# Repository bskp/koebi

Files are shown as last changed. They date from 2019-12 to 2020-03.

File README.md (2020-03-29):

Köbi: Robotic Puppeteering
==========================

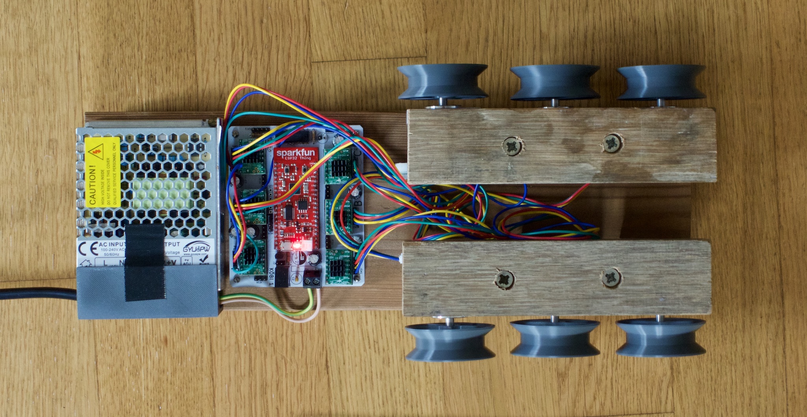
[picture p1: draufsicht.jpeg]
Setup


Köbi is a 6-channel wireless stepper controller consisting of a [SparkFun ESP32 Thing](https://www.sparkfun.com/products/13907) (red) and a **breakout shield** (white). The latter is inspired by [RAMPS](https://reprap.org/wiki/Arduino_Mega_Pololu_Shield) and accomodates six stepper motor drivers ([TMC2130 StepSticks](https://shop.watterott.com/SilentStepStick-TMC2130), green), optical endstop sensors and fan control.

The software on the ESP32 provides an [OSC (Open Sound Control)](https://en.wikipedia.org/wiki/Open_Sound_Control) server. This, in combination with a matching tablet GUI for the modular [TouchOSC](https://hexler.net/products/touchosc) app allows easy control of the steppers (which are the six thread spools).

Alternatively, the module can be controlled by any other OSC client. The OSC endpoints are documented at the [end of this page](#osc-api).

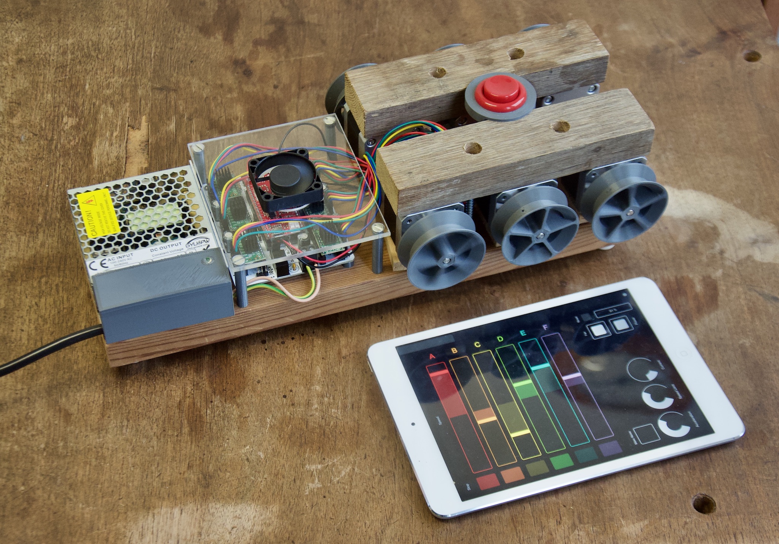
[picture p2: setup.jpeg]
No strings attached!

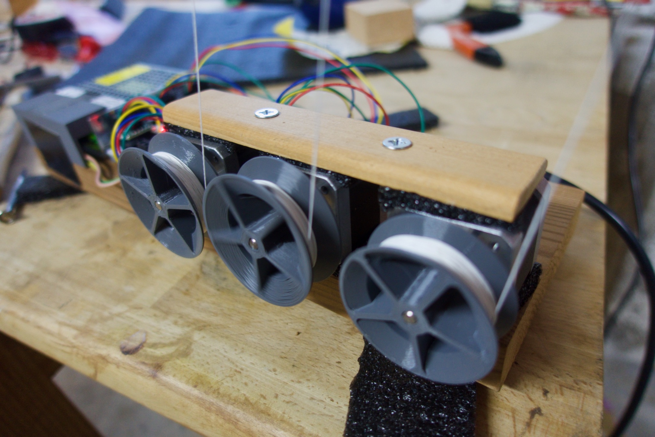
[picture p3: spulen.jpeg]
Spindles with threads


Features
--------

- 500g per thread
- Velocities up to 2m/s
- Wireless control
- Sub-centimeter precision
- (Almost) unlimited thread lengths
- Position and speed feedback for every channel
- Self-calibration using optical markers on the threads (TODO)
- Motor drivers configured using SPI, allowing for:
    - Microstepping reconfiguration (during operation)
    - Current control
    - Load estimation (TODO)
    - Count of missed steps if overload occurs (TODO)
- Easily extendable code written in [Micropython](https://micropython.org)
- Wireless console (WEBREPL) and code update (FTP)
- Additional I2C / SPI / GPIOs broken out

There are a ton of things you can hook it to. Feel free to reuse!

Software + Firmware
-------------------

The ESP32-Board runs a **special build** of the Micropython firmware due to two requirements:

- The PWM hardware module, which generates the **pulses for the  stepper motors**, is currently not supported by Micropython. This special build includes a Python module supporting it, implemented in C: The [MCPWM](https://github.com/bskp/micropython_esp32_mcpwm) module.

- The Python module for the **Trinamic TMC steppper drivers** (which holds names and descriptions to dozens of its registers) had to be frozen in order to save memory: The [TMC]() module. (TODO: Not published yet)

How much do you need? To get you started with the software, each of this three guides covers a different level:
1. **[Getting started](getting_started.md)**: Setup and interact with Köbi _using a tablet_ and the default OSC API
2. **[Hacking](hacking.md)**: Extend Köbis functionality _by modifying the Micropython_ code running the ESP32
3. **[Developing](developing.md)**: Modify the _Micropython firmware (written in C)_ to improve on the modules [MCPWM]() or [TMC](). These are part of the modified Micropython built, ie. "frozen"

Hardware
--------

This repo also supplies you with everything needed to build your own Köbi.

### Bill of Ordering Materials

| Thing | Brand | Part | Source | Price |
|---|---|---|---|---|
| Steppers (5-pack) | Hanpose  | 17HS4401  | AliExpress | 38.-  |
| Voltage Supply (120W) | GYU&PW | S-120-24  | AliExpress | 13.-  |
| ESP32 Thing | SparkFun | DEV-13907 | [bastelgarage](https://www.bastelgarage.ch/sparkfun-esp32-thing) | 22.- |

SN74LS138N

- bom: steppers, supply, esp32, tmcs, pcb/components, wall plug

### 3D Printed Parts
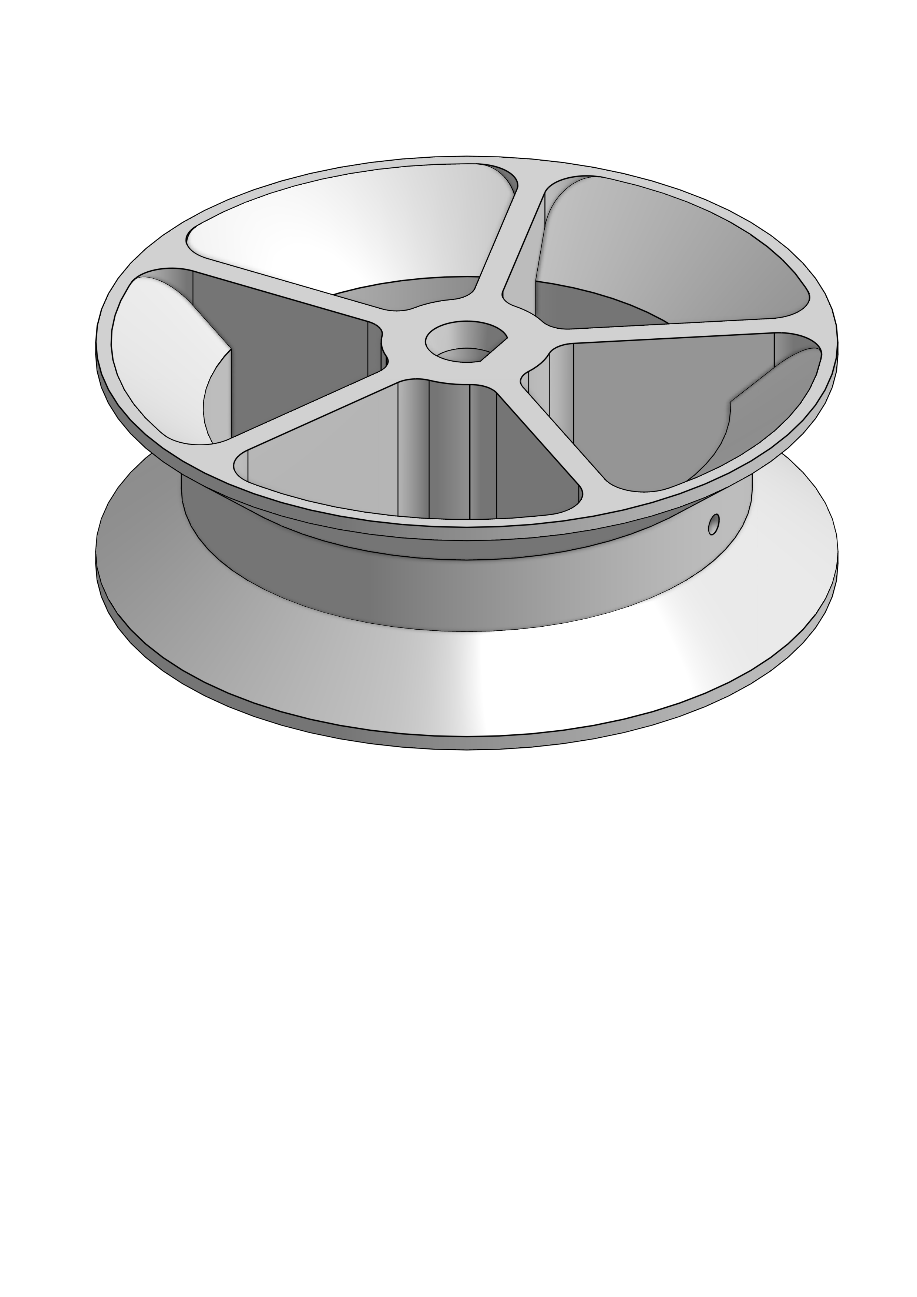
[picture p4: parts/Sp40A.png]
Thread Spool (40mm)

**Thread Spool (40mm)**: [.stl](parts/Sp40A.stl)
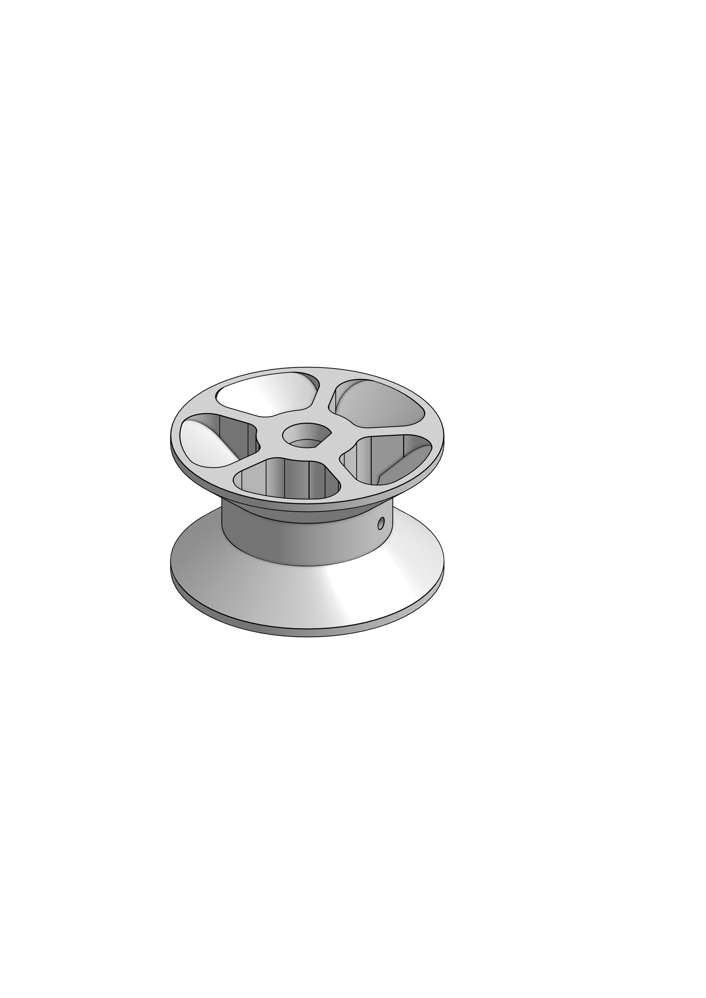
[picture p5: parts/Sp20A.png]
Thread Spool (20mm)

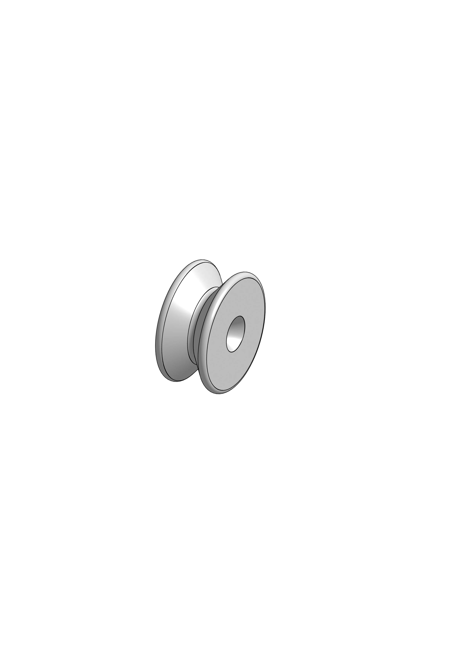
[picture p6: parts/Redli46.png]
Pulley

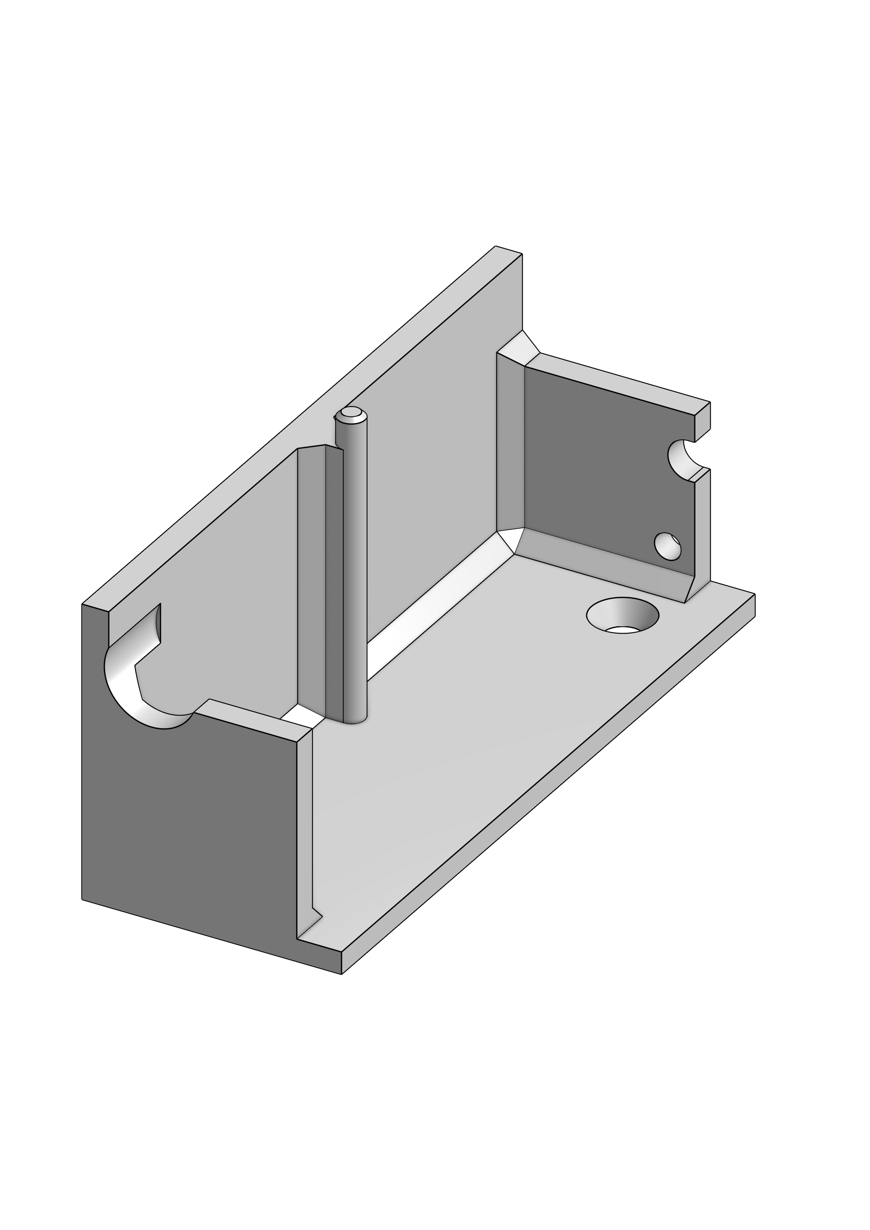
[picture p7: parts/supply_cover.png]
Voltage Supply Cover

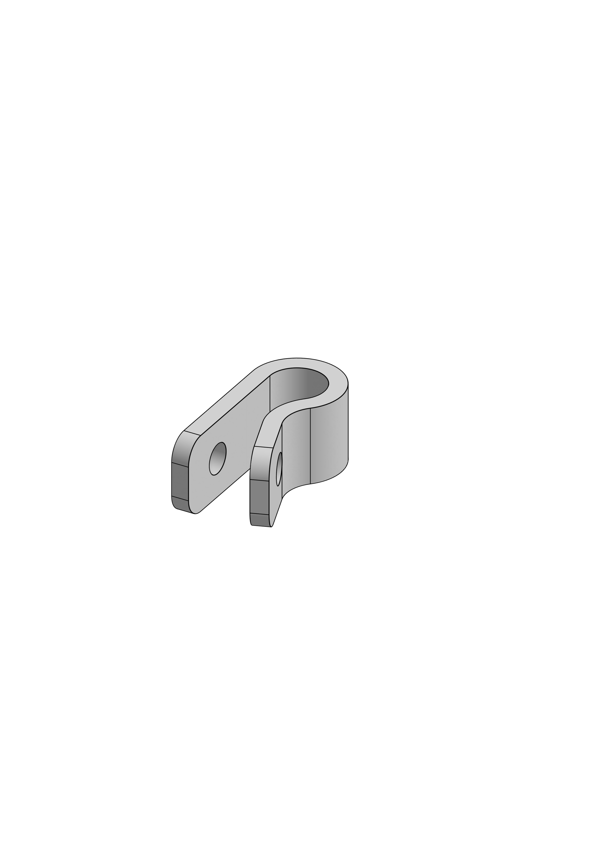
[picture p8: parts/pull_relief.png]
Pull Relief

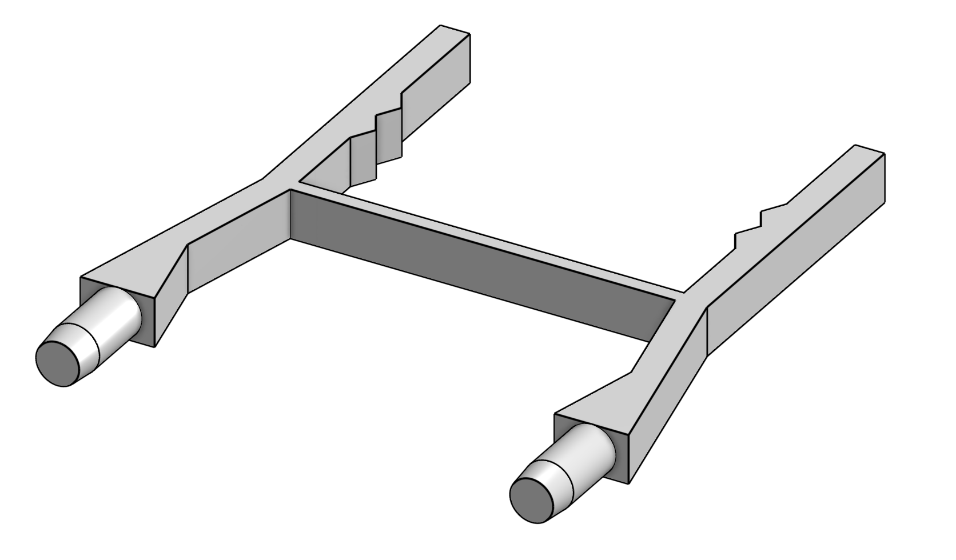
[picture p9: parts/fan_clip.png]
Poor Man's Fan Holder


- stl, link zu onshape

### Printed Circuit Board
- PCB-Daten als pdf, gerber und kicad.

Ideas
-----

- [x] Coordinated 2-axis movements
- [ ] Load visualization
- [ ] Presets with persistent storage
- [ ] Self-calibration with markers
- [x] Sequencer (Sine and jitter movements)
- [x] Coordinated movements for more than 2 axes
- [ ] Inverse kinematics

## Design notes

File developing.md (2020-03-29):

# Extend the Micropython Firmware

If you want to "freeze" a python module to free up RAM, or if you want to extend any of the frozen/native modules ``TMC`` or ``MCPWM``, you'll need to re-compile the firmware.

The process is fully described in the [esp32 port's README.md](https://github.com/micropython/micropython/blob/master/ports/esp32/README.md), but is mostly already taken care of. Start by initializing this repo's submodules:

~~~ bash
$ git submodule update --init --recursive
~~~

This clones the nested repos at ``/firmware/frameworks/``, which are the following projects:

### Micropython
The [referenced micropython fork](https://github.com/bskp/micropython_esp32_mcpwm/tree/micropython-for-koebi) supports the ESP32's **MCPWM**-Module, standing for _Motor control Pulse-Width-Modulation_. This was required to have enough PWM outputs available (6 modules).  
Read more about the MCPWM in [Espressif's API documentation](https://docs.espressif.com/projects/esp-idf/en/latest/esp32/api-reference/peripherals/mcpwm.html)!

### ESP-IDF
For better MCPWM-frequency update behaviour, we use a [minimally modified](https://github.com/espressif/esp-idf/compare/release/v3.3...bskp:dev-mcpwm-synched-updates) variant of the esp-idf, v3.3.1.

The _Micropython ESP32 port_'s Makefile located at ``firmware/frameworks/micropython/ports/esp32`` should already have the correct commit referenced, which was checked out while initializing the submodules:

~~~ Makefile
...
# The git hash of the currently supported ESP IDF version.
# These correspond to v3.3.1 and v4.0.
ESPIDF_SUPHASH_V3 := cc02b01ea59e112e6ccf7fc3b66f3624f5d41167  # patched MCPWM update behaviour, based upon v3.3.1
ESPIDF_SUPHASH_V4 := 463a9d8b7f9af8205222b80707f9bdbba7c530e1
...
~~~

### Frozen Modules

The last puzzle piece is the stepper-driver specific python package ``tmc_control``, located at ``firmware/src_frozen``.

Since it contains mappings for _almost all_ of TMC2130's registers, this uses up a ton of RAM if loaded dynamically. Therefore, they are better ["frozen" into the Micropython](http://docs.micropython.org/en/latest/reference/constrained.html) firmware.

This is achieved by copying the modules from ``/firmware/src_frozen`` to ``/firmware/frameworks/micropython/ports/esp32/modules``:

- tmc_control
    - __init__.py
    - axis.py
    - tmc2130.py
- uasyncio
    - __init__.py
    - core.py
- uftpd.py

(Actually, the latter two, ``uasyncio`` and ``uftpd`` should already be there.)

### Configuration

The remaining steps are explained in more detail in ``ports/esp32/README.me``. 

The environment variables for the build process are defined in ``GNUMakefile``, which takes precedence over ``Makefile``:

~~~ Makefile
ESPIDF = ../../../esp-idf
BOARD = GENERIC
PORT = /dev/tty.usbserial-DN05LWXG
FLASH_MODE = dio
FLASH_SIZE = 4MB
CROSS_COMPILE = $(ESPIDF)/xtensa-esp32-elf/bin/xtensa-esp32-elf-

include Makefile
~~~~

Make sure to adjust the ``PORT`` according to your setup!

### Compiling

See the [esp32 port's README.md](https://github.com/micropython/micropython/blob/master/ports/esp32/README.md) for troubleshooting.

~~~ bash
$ cd mpy-cross
$ make mpy-cross

$ cd ../ports/esp32
$ make clean
$ make submodules
$ make deploy # erases the ESP32's firmware and uploads!
~~~

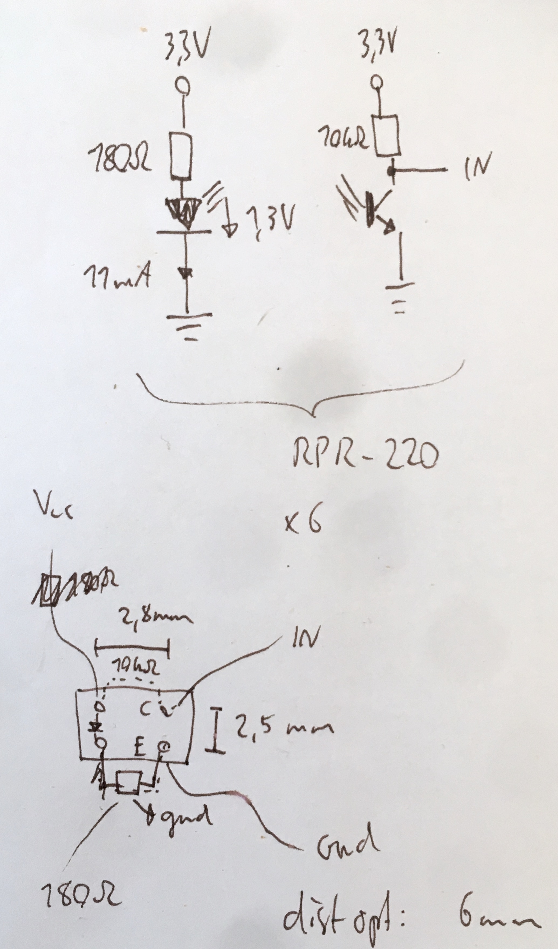
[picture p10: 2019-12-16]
pcb/endstopp.jpeg

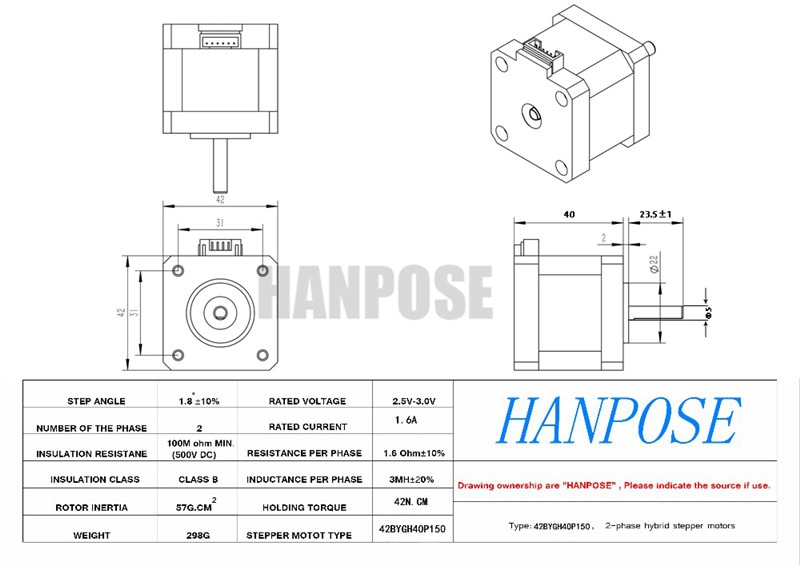
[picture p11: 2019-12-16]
datasheets/Hanpose 17HS4401.jpg

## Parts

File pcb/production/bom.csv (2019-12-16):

ID | Bezeichner | Gehäuse | Stückzahl | Bezeichnung | Anbieter und Referenz
1 | REF**,REF**,REF**,REF** | MountingHole_2.5mm | 4 | MountingHole_2.5mm
2 | JSPI | PinHeader_1x06_P2.54mm_Vertical | 1 | Conn_01x06_Male
3 | JAUX,JSM2,JSM6,JSM5,JSM4,JSM3,JSM1 | PinHeader_1x04_P2.54mm_Vertical | 7 | Conn_01x04_Male
4 | B0 | ESP32_THING | 1 | ESP32_THING_W_ANT_KEEPOUT
5 | U1 | DIP-16_W7.62mm | 1 | 74LS138
6 | B6,B5,B4,B3,B2,B1 | StepStick | 6 | SilentStepStick
7 | JP6,JP5,JP16,JP15,JP14,JP13,JP12,JP11,JP10,JP7,JP9,JP8,JP1 | SolderJumper-3_P1.3mm_Bridged12_RoundedPad1.0x1.5mm | 13 | SolderJumper_3_Bridged12
8 | JES2,JES6,JES5,JES4,JES3,JES1 | PinHeader_1x03_P2.54mm_Vertical | 6 | Conn_01x03_Male
9 | C5,C9,C8,C7,C6,C3,C4,C1 | CP_Radial_D8.0mm_P3.50mm | 8 | 100u
10 | JRST1 | PinHeader_1x01_P2.54mm_Vertical | 1 | Conn_01x01_Male
11 | _C1 | C_Radial_D6.3mm_H5.0mm_P2.50mm | 1 | 1n
12 | U2 | Converter_DCDC_TRACO_TSR-1_THT | 1 | TSR_1-2450
13 | R5 | R_Axial_DIN0207_L6.3mm_D2.5mm_P7.62mm_Horizontal | 1 | 1k
14 | R4,R3 | R_Axial_DIN0207_L6.3mm_D2.5mm_P7.62mm_Horizontal | 2 | 4k7
15 | R2 | R_Axial_DIN0207_L6.3mm_D2.5mm_P7.62mm_Horizontal | 1 | 10k
16 | R1 | R_Axial_DIN0207_L6.3mm_D2.5mm_P7.62mm_Horizontal | 1 | 100kOhm
17 | Q2,Q1 | TO-92_Inline | 2 | BC547
18 | JP4,JP3,JP2 | SolderJumper-3_P1.3mm_Open_RoundedPad1.0x1.5mm | 3 | SolderJumper_3_Open
19 | J3 | PinHeader_1x02_P2.54mm_Vertical | 1 | Conn_01x02_Male
20 | JI2C1 | PinHeader_1x04_P2.54mm_Vertical | 1 | Conn_01x04_Female
21 | J1 | TerminalBlock_RND_205-00232_1x02_P5.08mm_Horizontal | 1 | Screw_Terminal_01x02
22 | F1 | Fuse_Bourns_MF-RHT1000 | 1 | Polyfuse
23 | C2 | C_Radial_D6.3mm_H5.0mm_P2.50mm | 1 | 100n

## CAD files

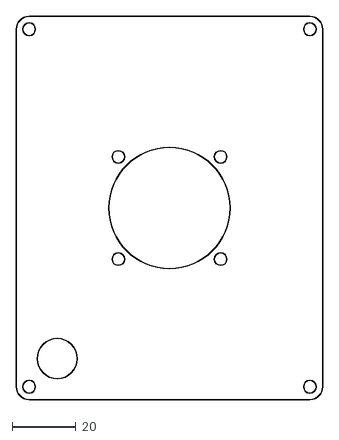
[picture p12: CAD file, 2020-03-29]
parts/pcb_cover.dxf
96.0 x 120.0

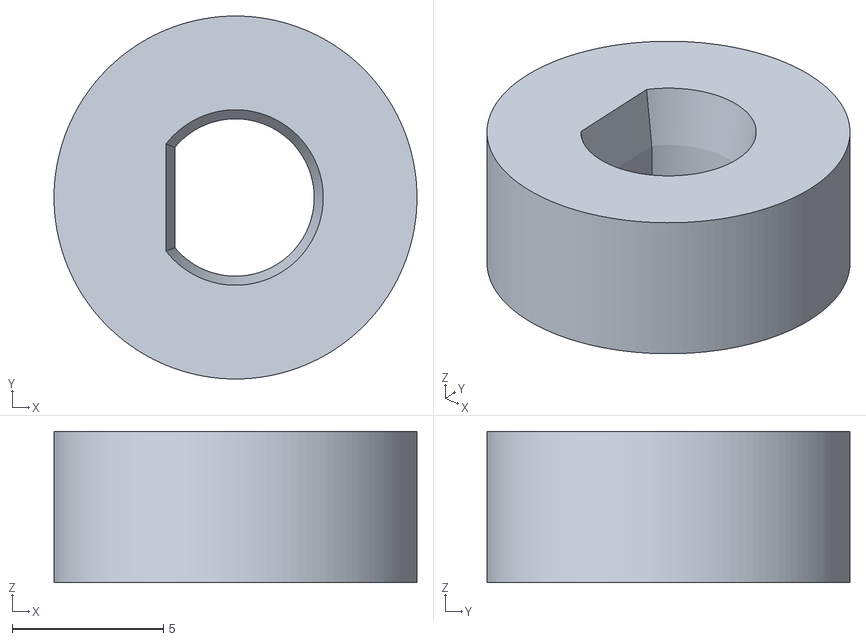
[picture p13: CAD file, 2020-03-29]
parts/kopp-46-52.stl
12.0 x 12.0 x 5.00

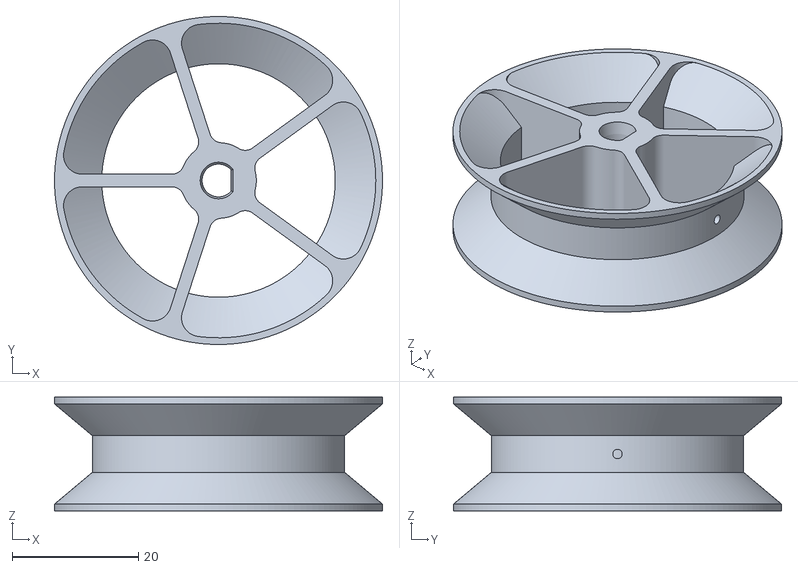
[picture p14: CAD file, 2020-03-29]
parts/Sp40A.stl
52.0 x 52.0 x 18.0

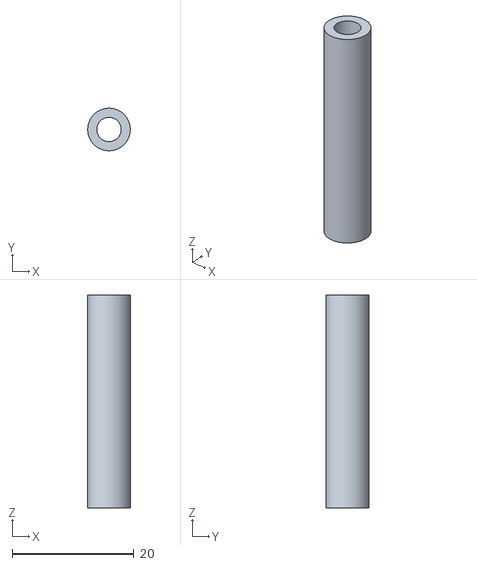
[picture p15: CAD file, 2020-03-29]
parts/spacer35.stl
7.00 x 7.00 x 35.0

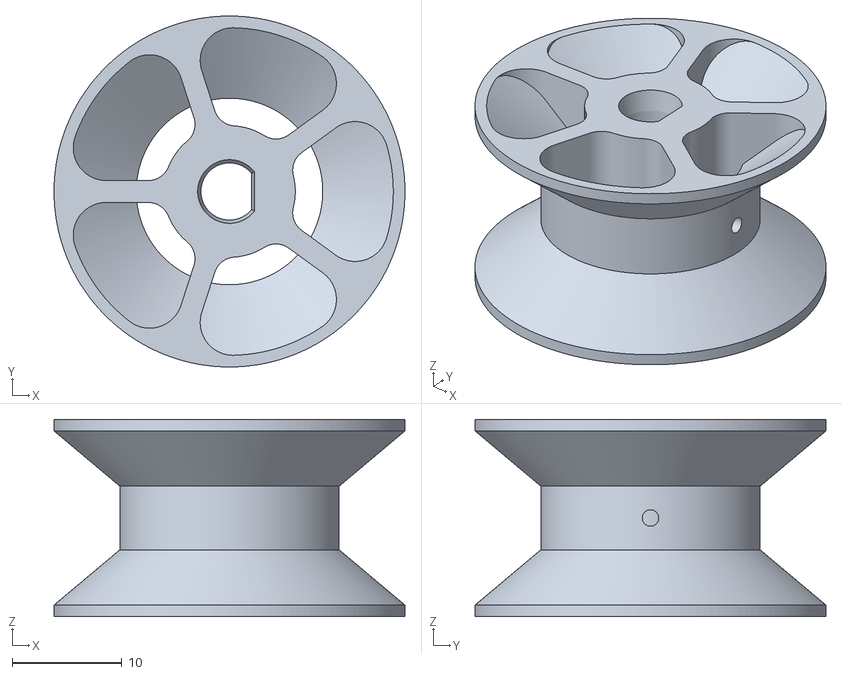
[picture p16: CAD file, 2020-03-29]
parts/Sp20A.stl
32.0 x 32.0 x 18.0

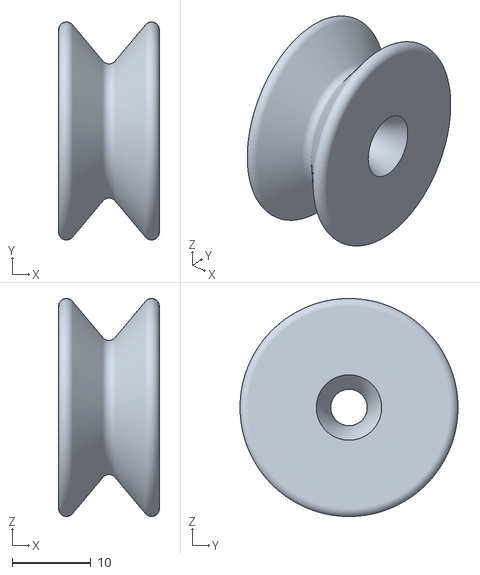
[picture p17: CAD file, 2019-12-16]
parts/Redli46.stl
12.8 x 27.6 x 27.6

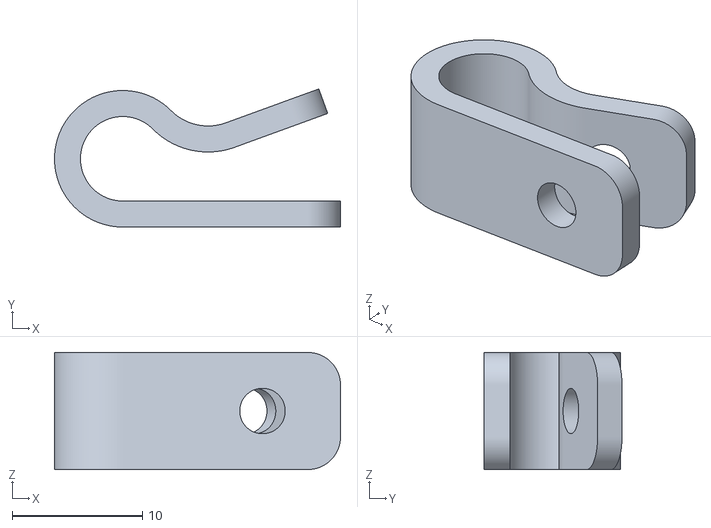
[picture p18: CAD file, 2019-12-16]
parts/pull_relief.stl
22.0 x 10.6 x 9.00

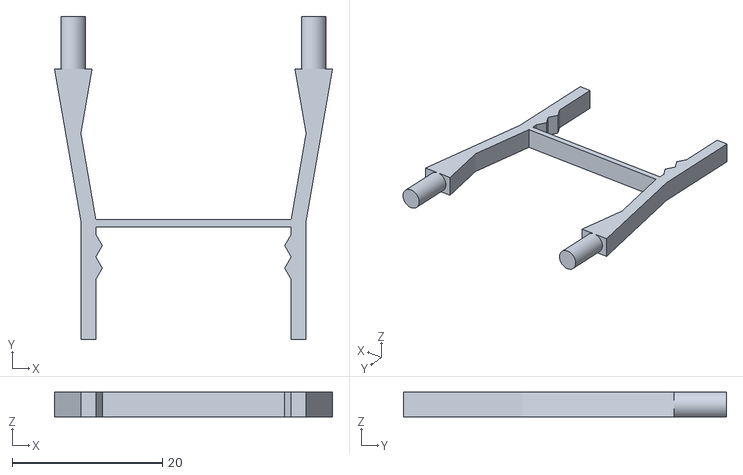
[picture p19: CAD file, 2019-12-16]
parts/fan_clip.stl
37.0 x 43.0 x 3.30

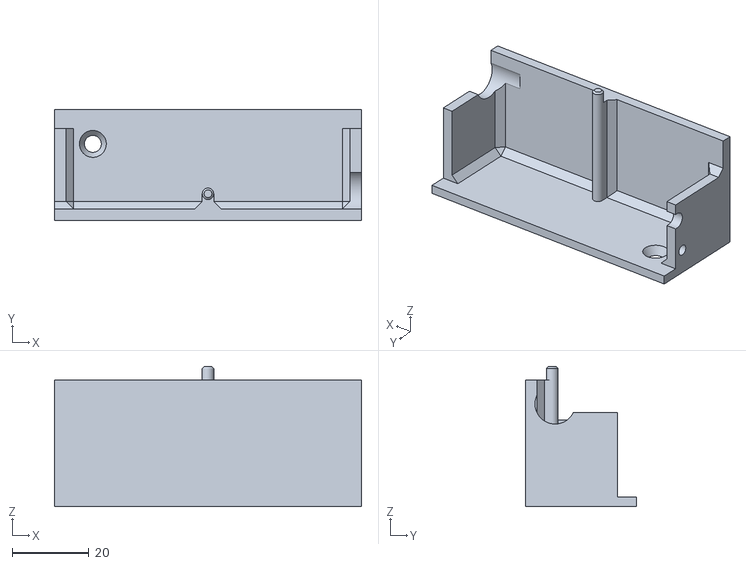
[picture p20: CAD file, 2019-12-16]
parts/supply_cover.stl
80.0 x 29.0 x 36.5

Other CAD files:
parts/kopp-45-53.stl

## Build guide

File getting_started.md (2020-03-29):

Setup + Interacting
===================

This section explains how to get koebi up and running with the default firmware and tablet GUI. This combination allows to control the **speed** and **position** of the six stepper motors **independently** or **pairwise coordinated moves**.

Firmware
--------

Use the [esptool](https://github.com/espressif/esptool) to flash this Micropython build on the ESP32. It is easily installed using pip:

```
$ pip install esptool
```

If you put Micropython on your board for the first time, it should be erased first:

```
$ esptool.py --chip esp32 --port /dev/ttyUSB0 erase_flash
```

After this, the custom firmware can be flashed:

```
$ cd (...)/koebi/firmware
$ esptool.py --chip esp32 --port /dev/ttyUSB0 --baud 406800 write_flash -z --flash_mode dio --flash_freq 40m 0x1000 firmware.bin
``` 

For more information, see the [official Micropython docs](https://micropython.org/download#esp32).

Setup the TouchOSC GUI
----------------------

- Install the [TouchOSC](https://hexler.net/products/touchosc) app on a tablet.  
It's a paid app (5.-, sorry about that)

- Install the application to edit layouts, [TouchOSC Editor](https://hexler.net/products/touchosc#downloads), on a computer (free)

- Transfer the ``koebi.touchosc`` (found in ``/gui``) to the tablet. The official documentation walks you through this for [iOS](https://hexler.net/docs/touchosc-configuration-layout-transfer-wifi?ios) and [Android](https://hexler.net/docs/touchosc-configuration-layout-transfer-wifi?android)

To complete the setup, you need to specify a few options on the tablet. Access these by tapping the **dot** at the **top right corner** in the TouchOSC app.

Set the following **Host**:

- Host: ``192.168.4.1`` (which is the ESP32's IP Address)
- Port (outgoing): ``8000``
- Port (incoming): ``9000``

And under **Options**:

- Send Ping (``/ping``): ``On``
- Delay: ``5s`` 

Finally, make sure to connect with the systems WiFi:
- Network name (SSID): ``koebi``
- No password / encryption

When opening TouchOSC, you should now be able to power up the motors and control them. 

Open Sound Control (OSC) API
============================

The tablet uses the following API to communicate with the ESP32. It is implemented in ``main.py`` and can be used by any other client within ``koebis``'s network to control it.  
 
**Feedback Behaviour**:

**Need more?** Read the [hacking guide](hacking.md).

Globals
-------

### ``/fan``
Enable or disable the fan cooling the stepper drivers (0/1)

### ``/power``
Enable or disable the stepper drivers output. Starts the fan upon enabling, and stops it upon disabling (0/1).  
**Heads up**: Always disable the stepper outputs before pulling koebi's cord. Otherwise, the Trinamic stepper drivers may **be permanently damaged due to overvoltage spikes**!

### ``/reset``
Trigger a software reset of the ESP32 board (0/1)

Stepper Motor Globals
---------------------

### ``/all/curr``
Set all steppers' run current, specified in milliamperes (100..1200). High values (>800) may lead to thermal shutdown in a heavy-use scenario.
### ``/all/acc``
Set all steppers' acceleration, in cm/s<sup>2</sup> (0.1…200)
### ``/all/vel_limit``
Set all stepper's max velocity, in cm/s (0…200)

## Individual Stepper Motor Commands
For each of the following endpoints, ``[motor]`` may be ``a``, ``b``, ``c``, ``d``, ``e`` or ``f``.

### ``/[motor]/vel``
Set a steppers velocity as a factor of the velocity limit (0 … 1).  
### ``/[motor]/zero``
Define a steppers current position as the new ``0.0``, ie. home position (0/1)
### ``/[motor]/end``
Define a steppers current position as the new ``1.0``, ie. end position (0/1)
### ``/[motor]/target``
Set a steppers target position as a factor of the motor's axis length (0…1)
### ``/[motor]/pos``
Get a steppers current position as a factor of the motor's axis length (0…1)

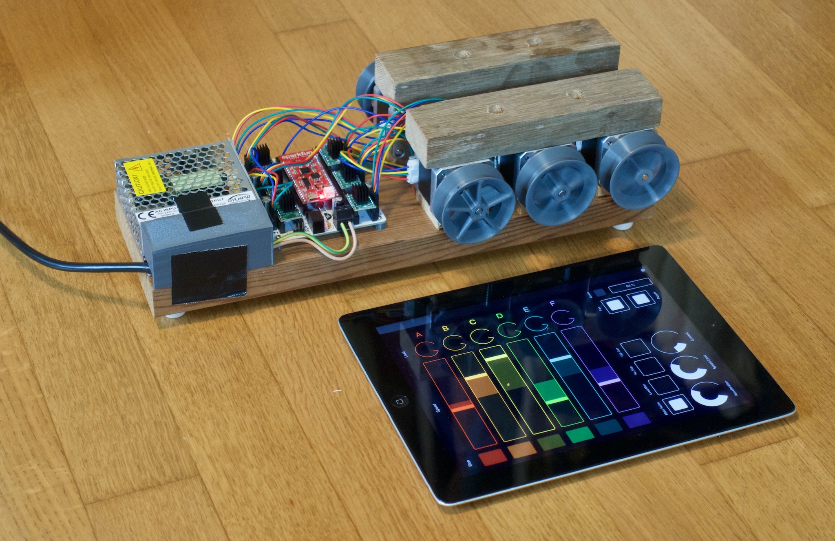
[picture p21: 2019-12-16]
setup_alt.jpeg

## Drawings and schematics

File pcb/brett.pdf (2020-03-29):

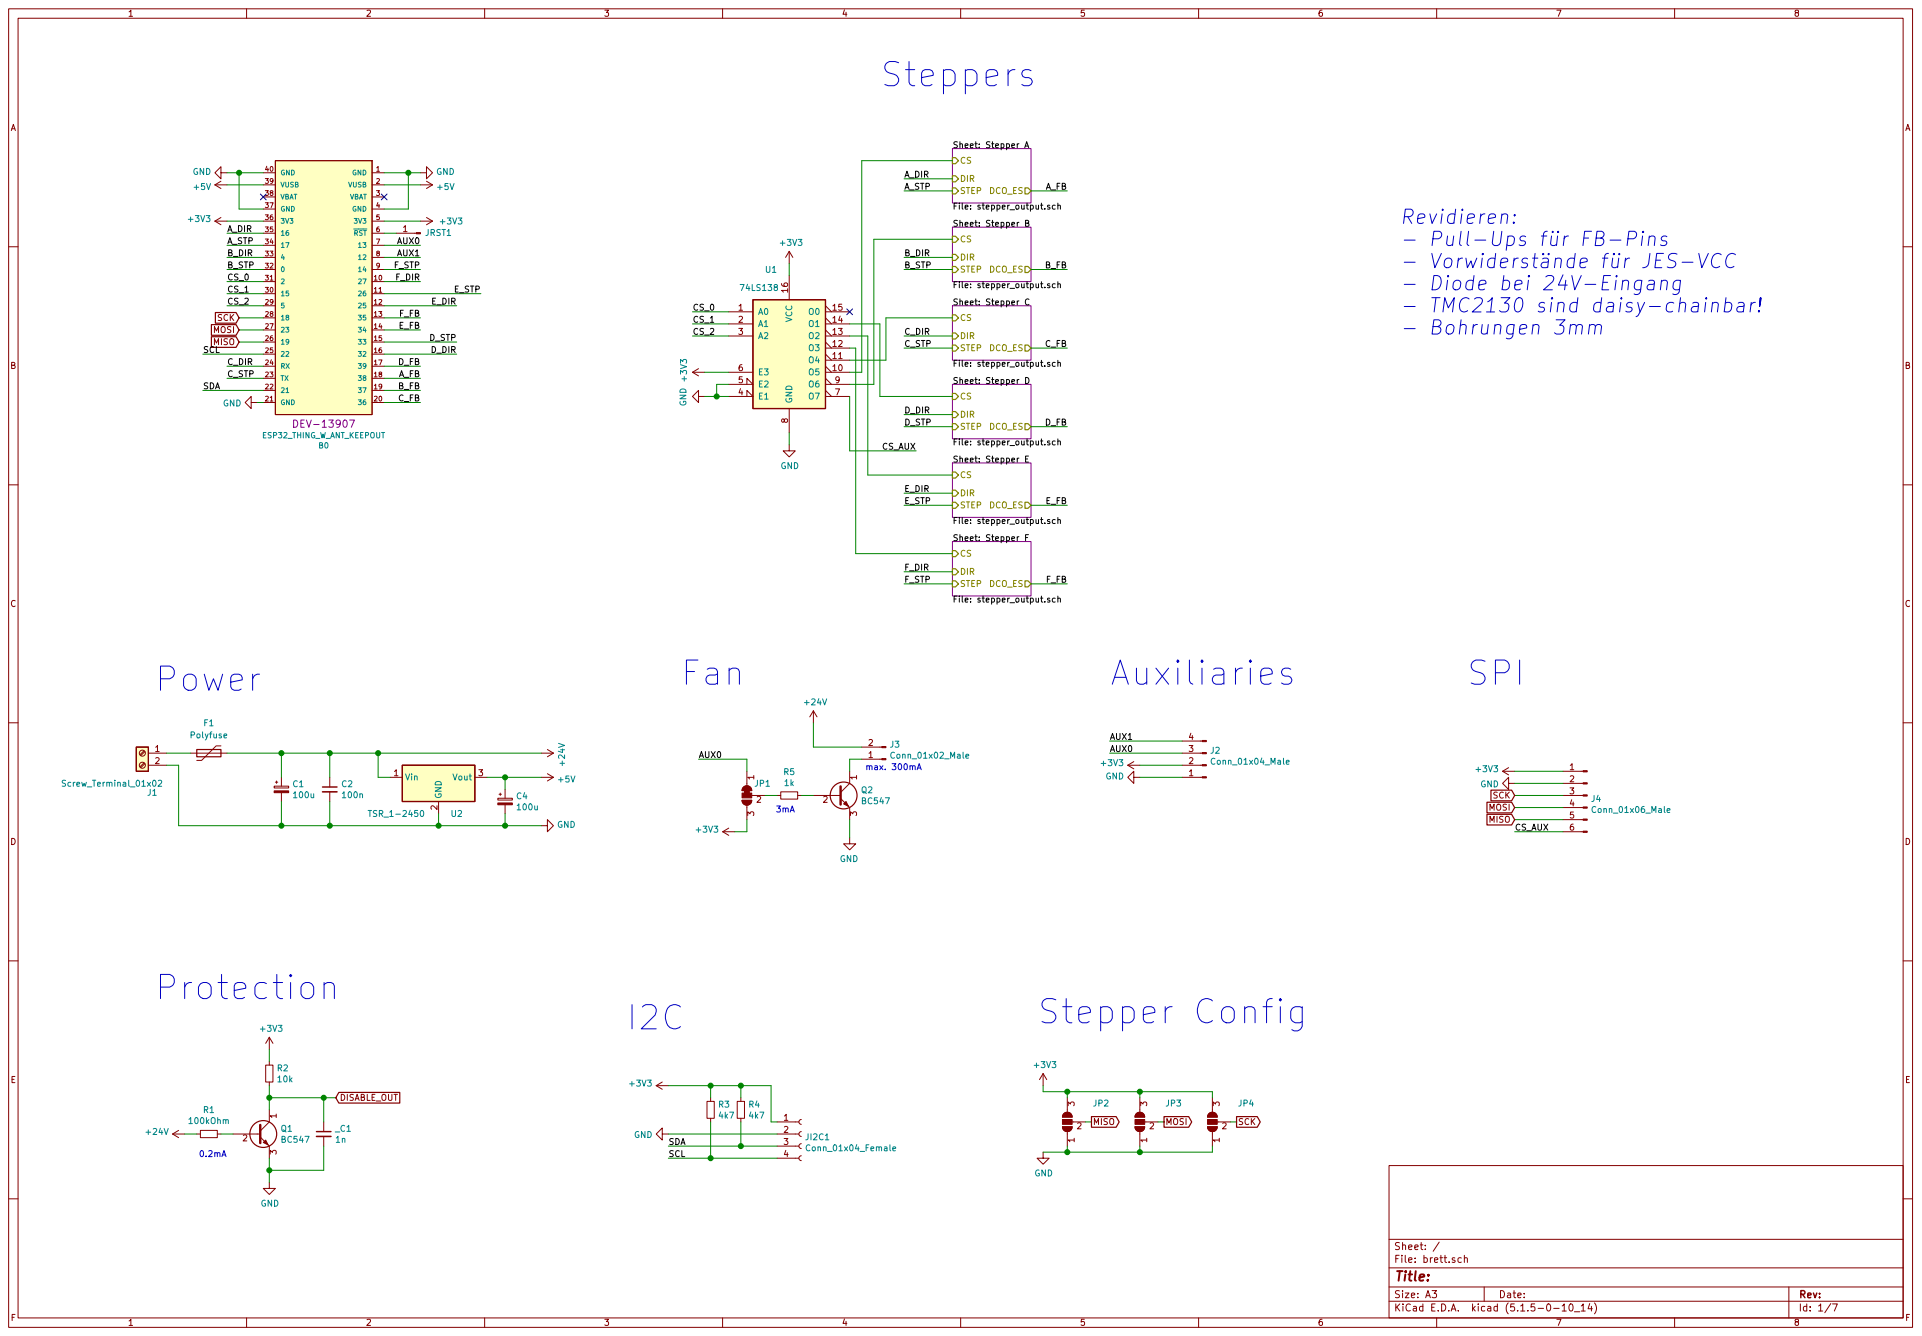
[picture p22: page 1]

Revidieren:
- Pull-Ups für FB-Pins
- Vorwiderstände für JES-VCC
- Diode bei 24V-Eingang
- TMC2130 sind daisy-chainbar!
- Bohrungen 3mm

Id: 1/7 Title: File: brett.sch Sheet: /

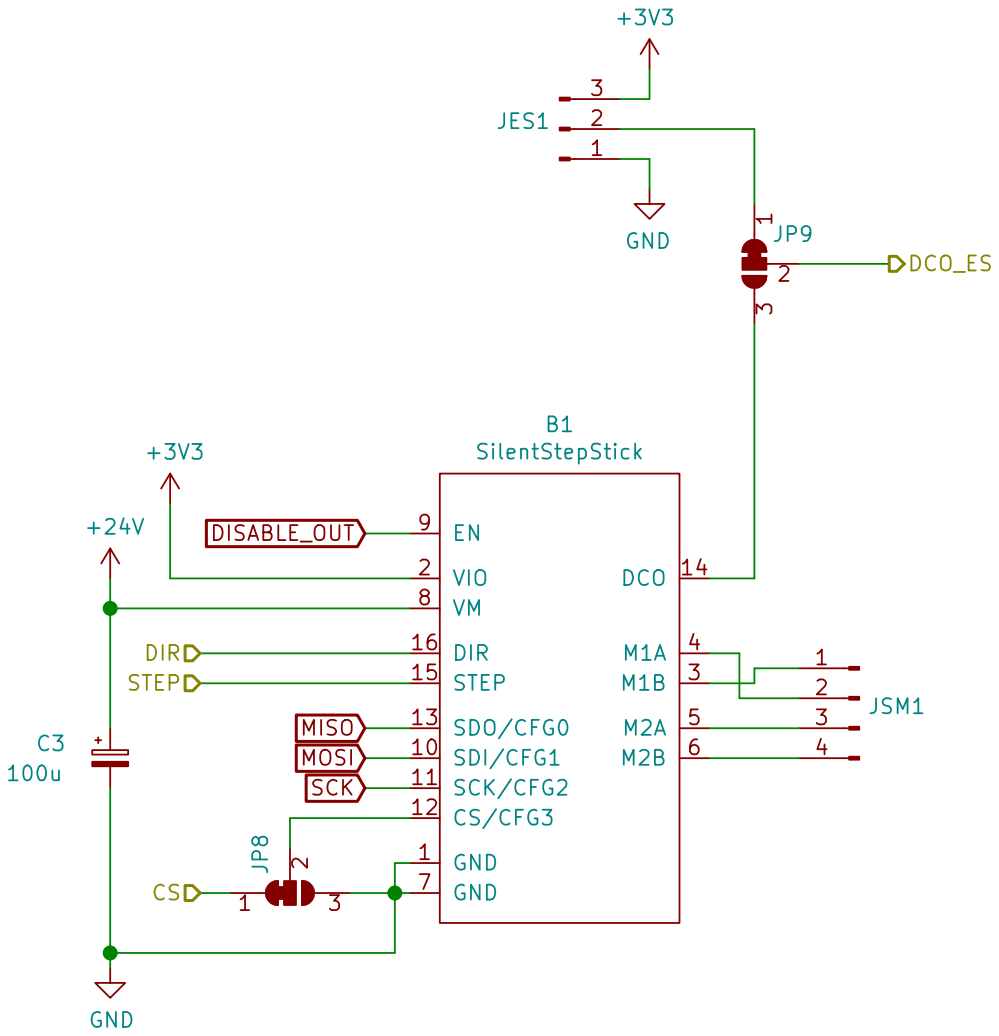
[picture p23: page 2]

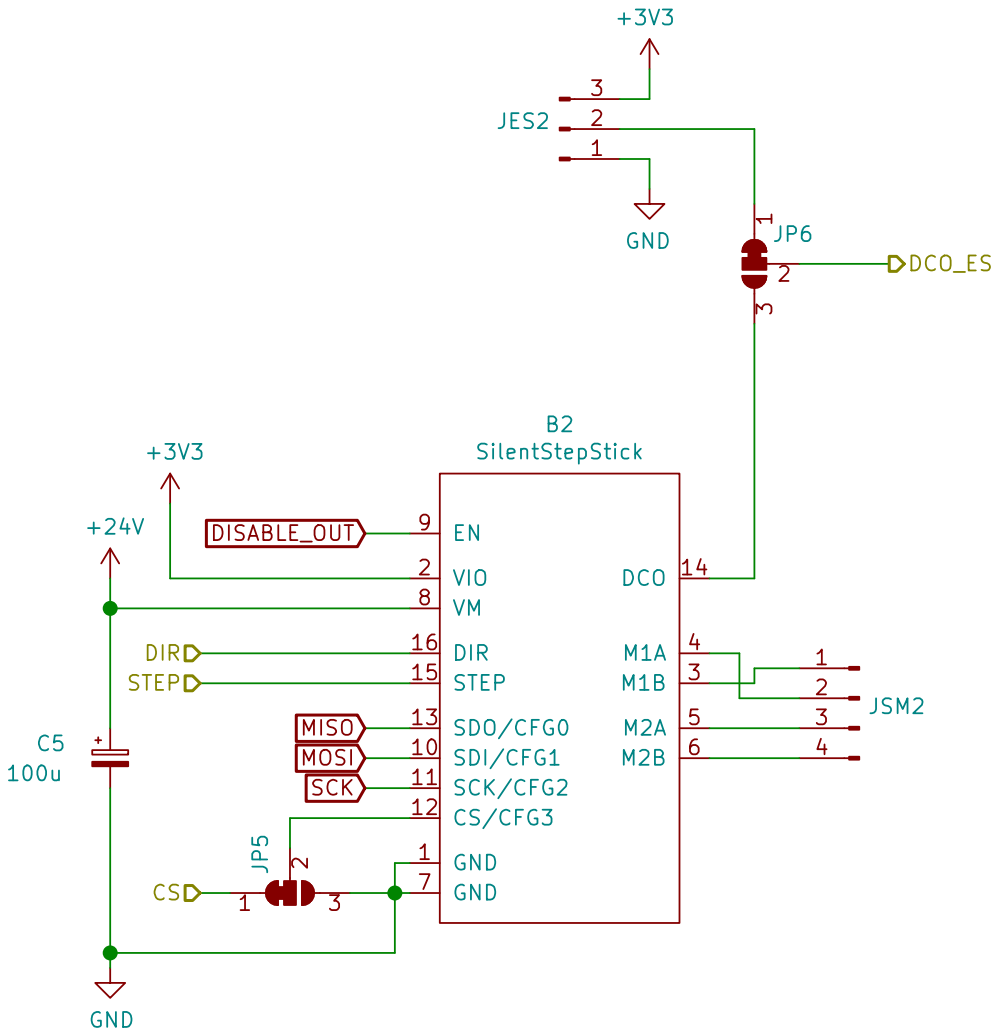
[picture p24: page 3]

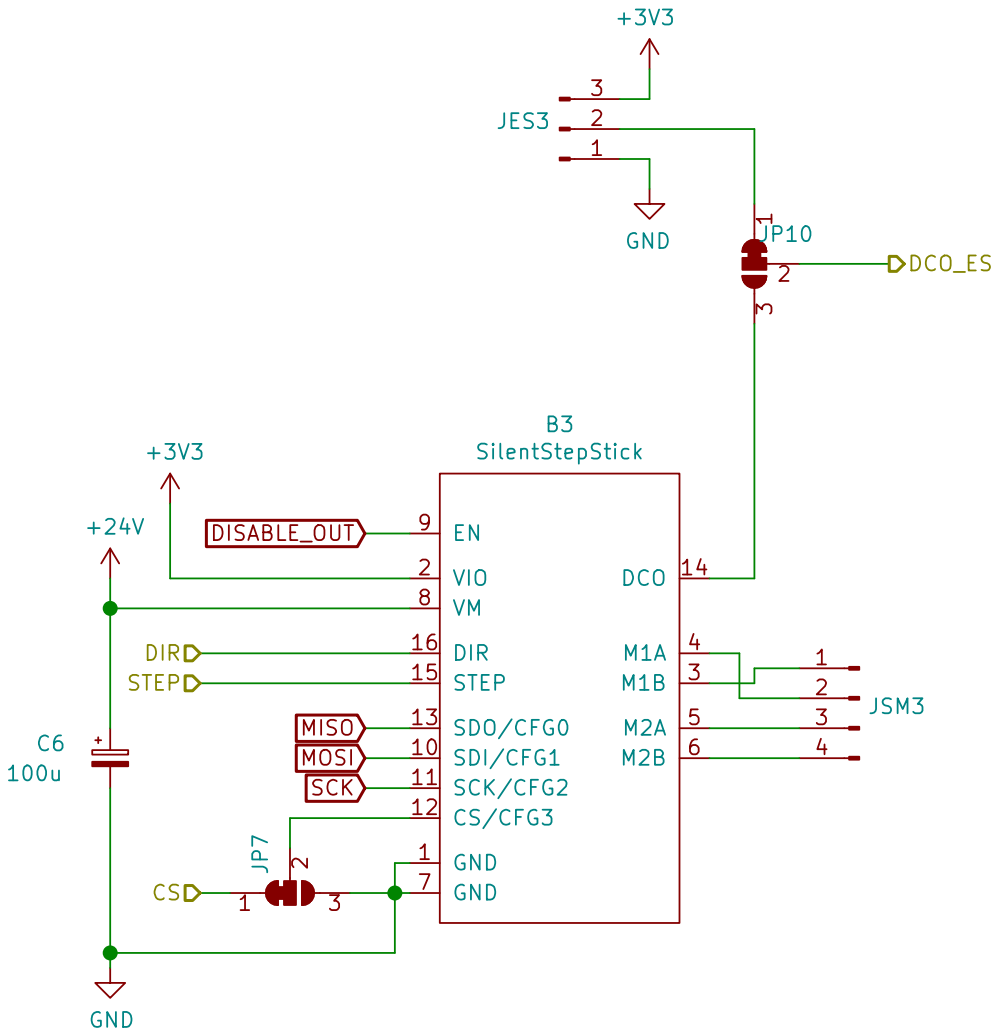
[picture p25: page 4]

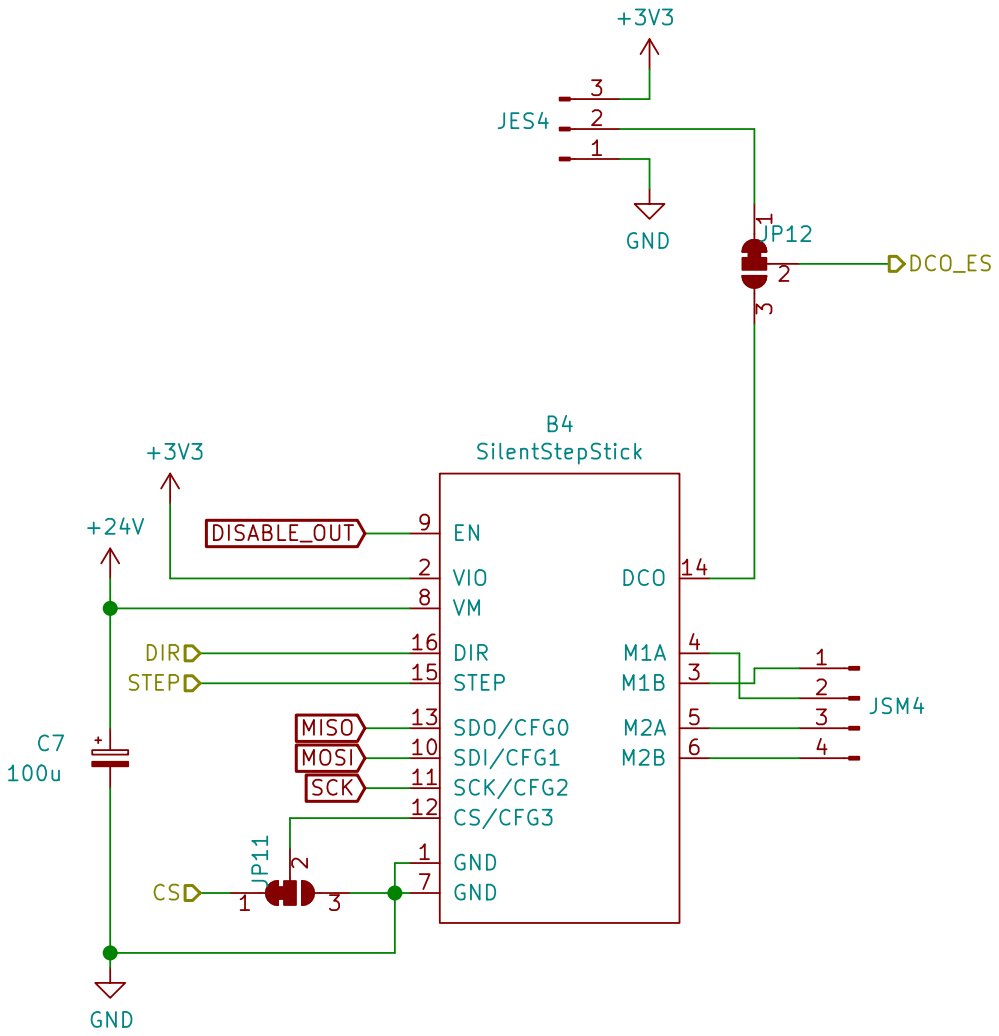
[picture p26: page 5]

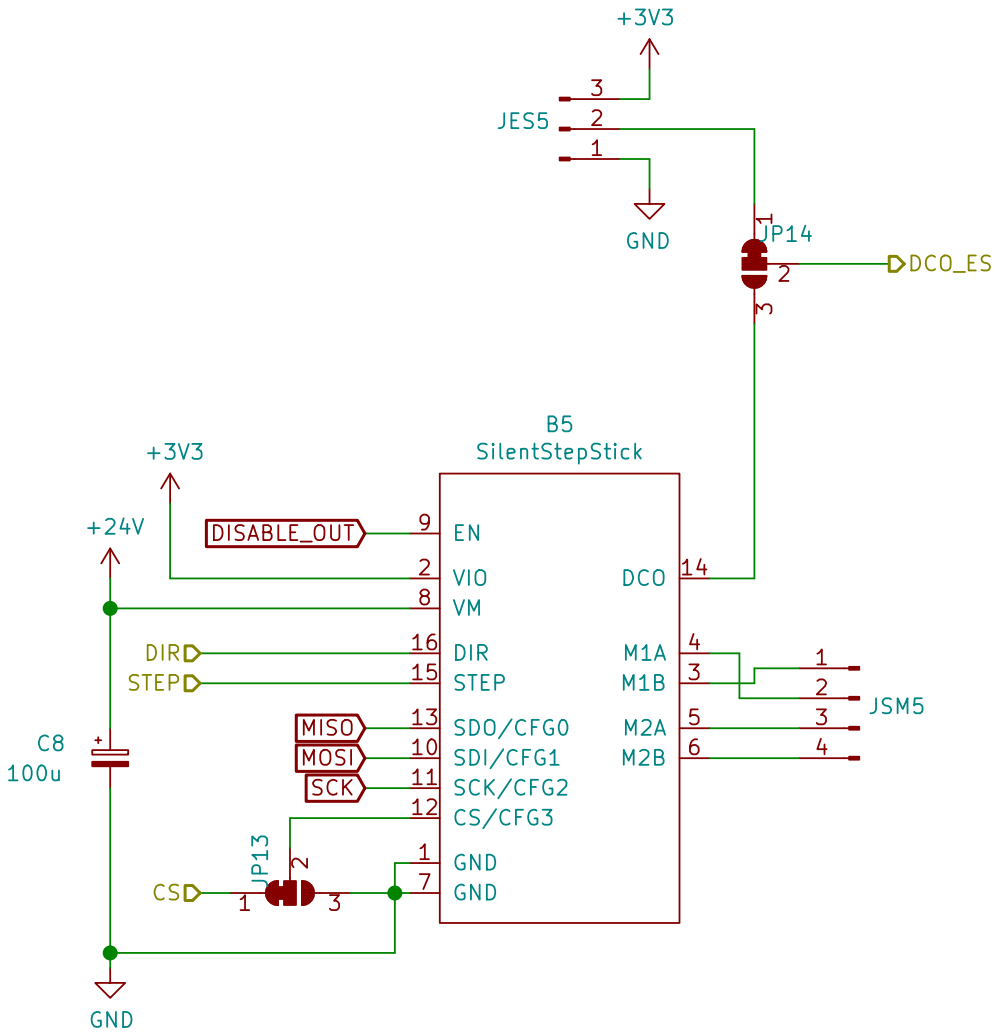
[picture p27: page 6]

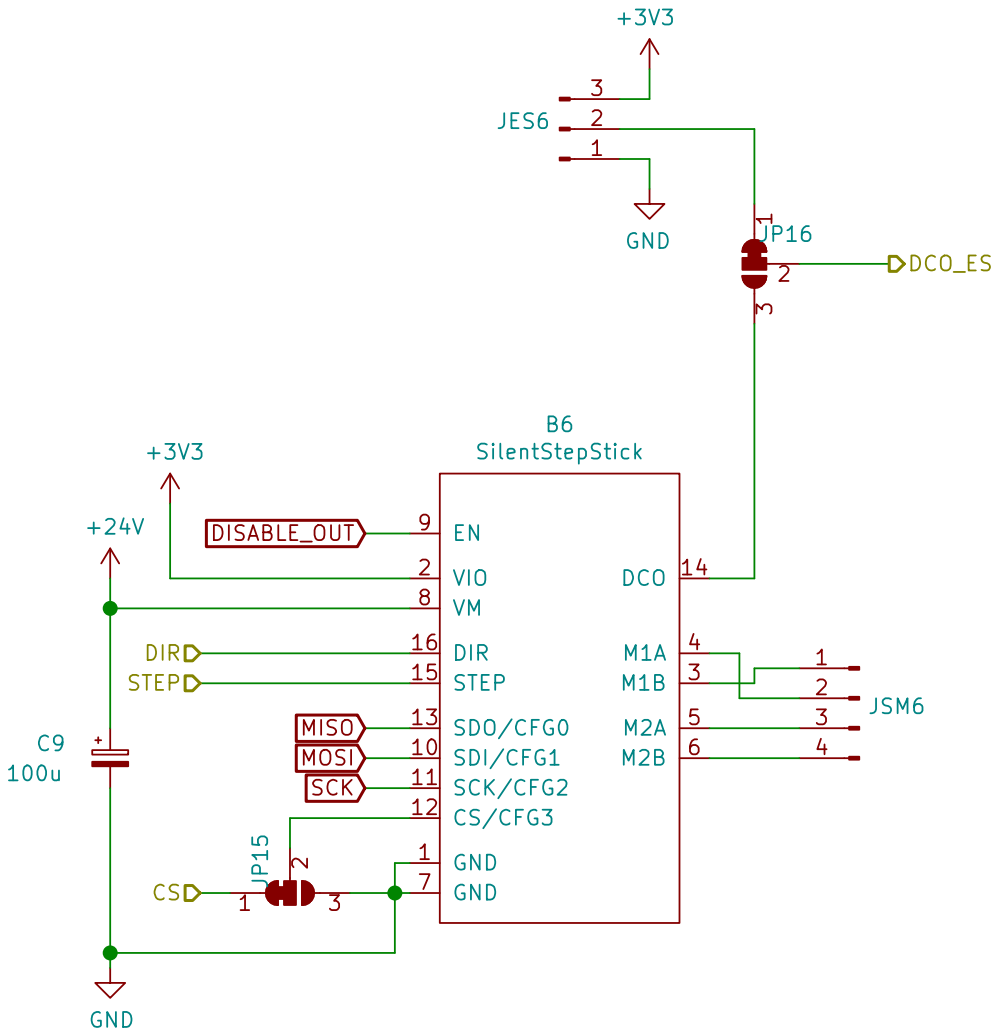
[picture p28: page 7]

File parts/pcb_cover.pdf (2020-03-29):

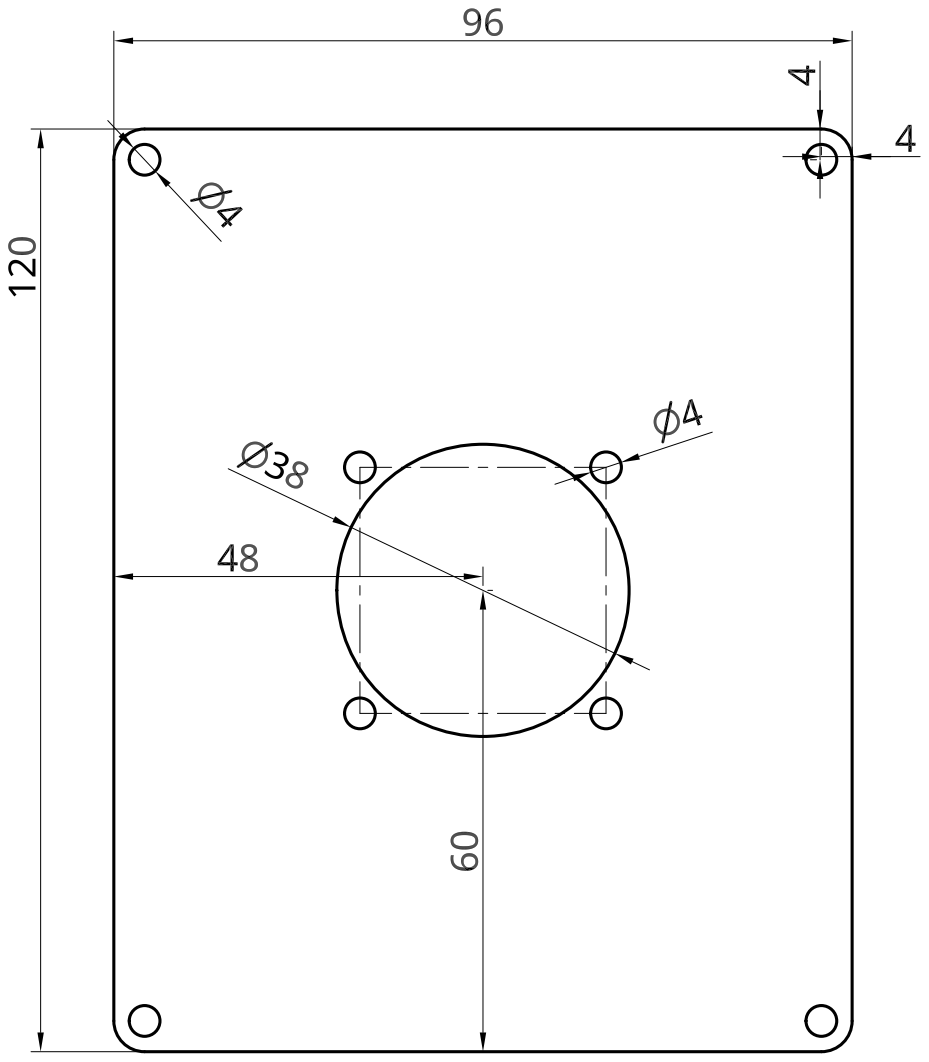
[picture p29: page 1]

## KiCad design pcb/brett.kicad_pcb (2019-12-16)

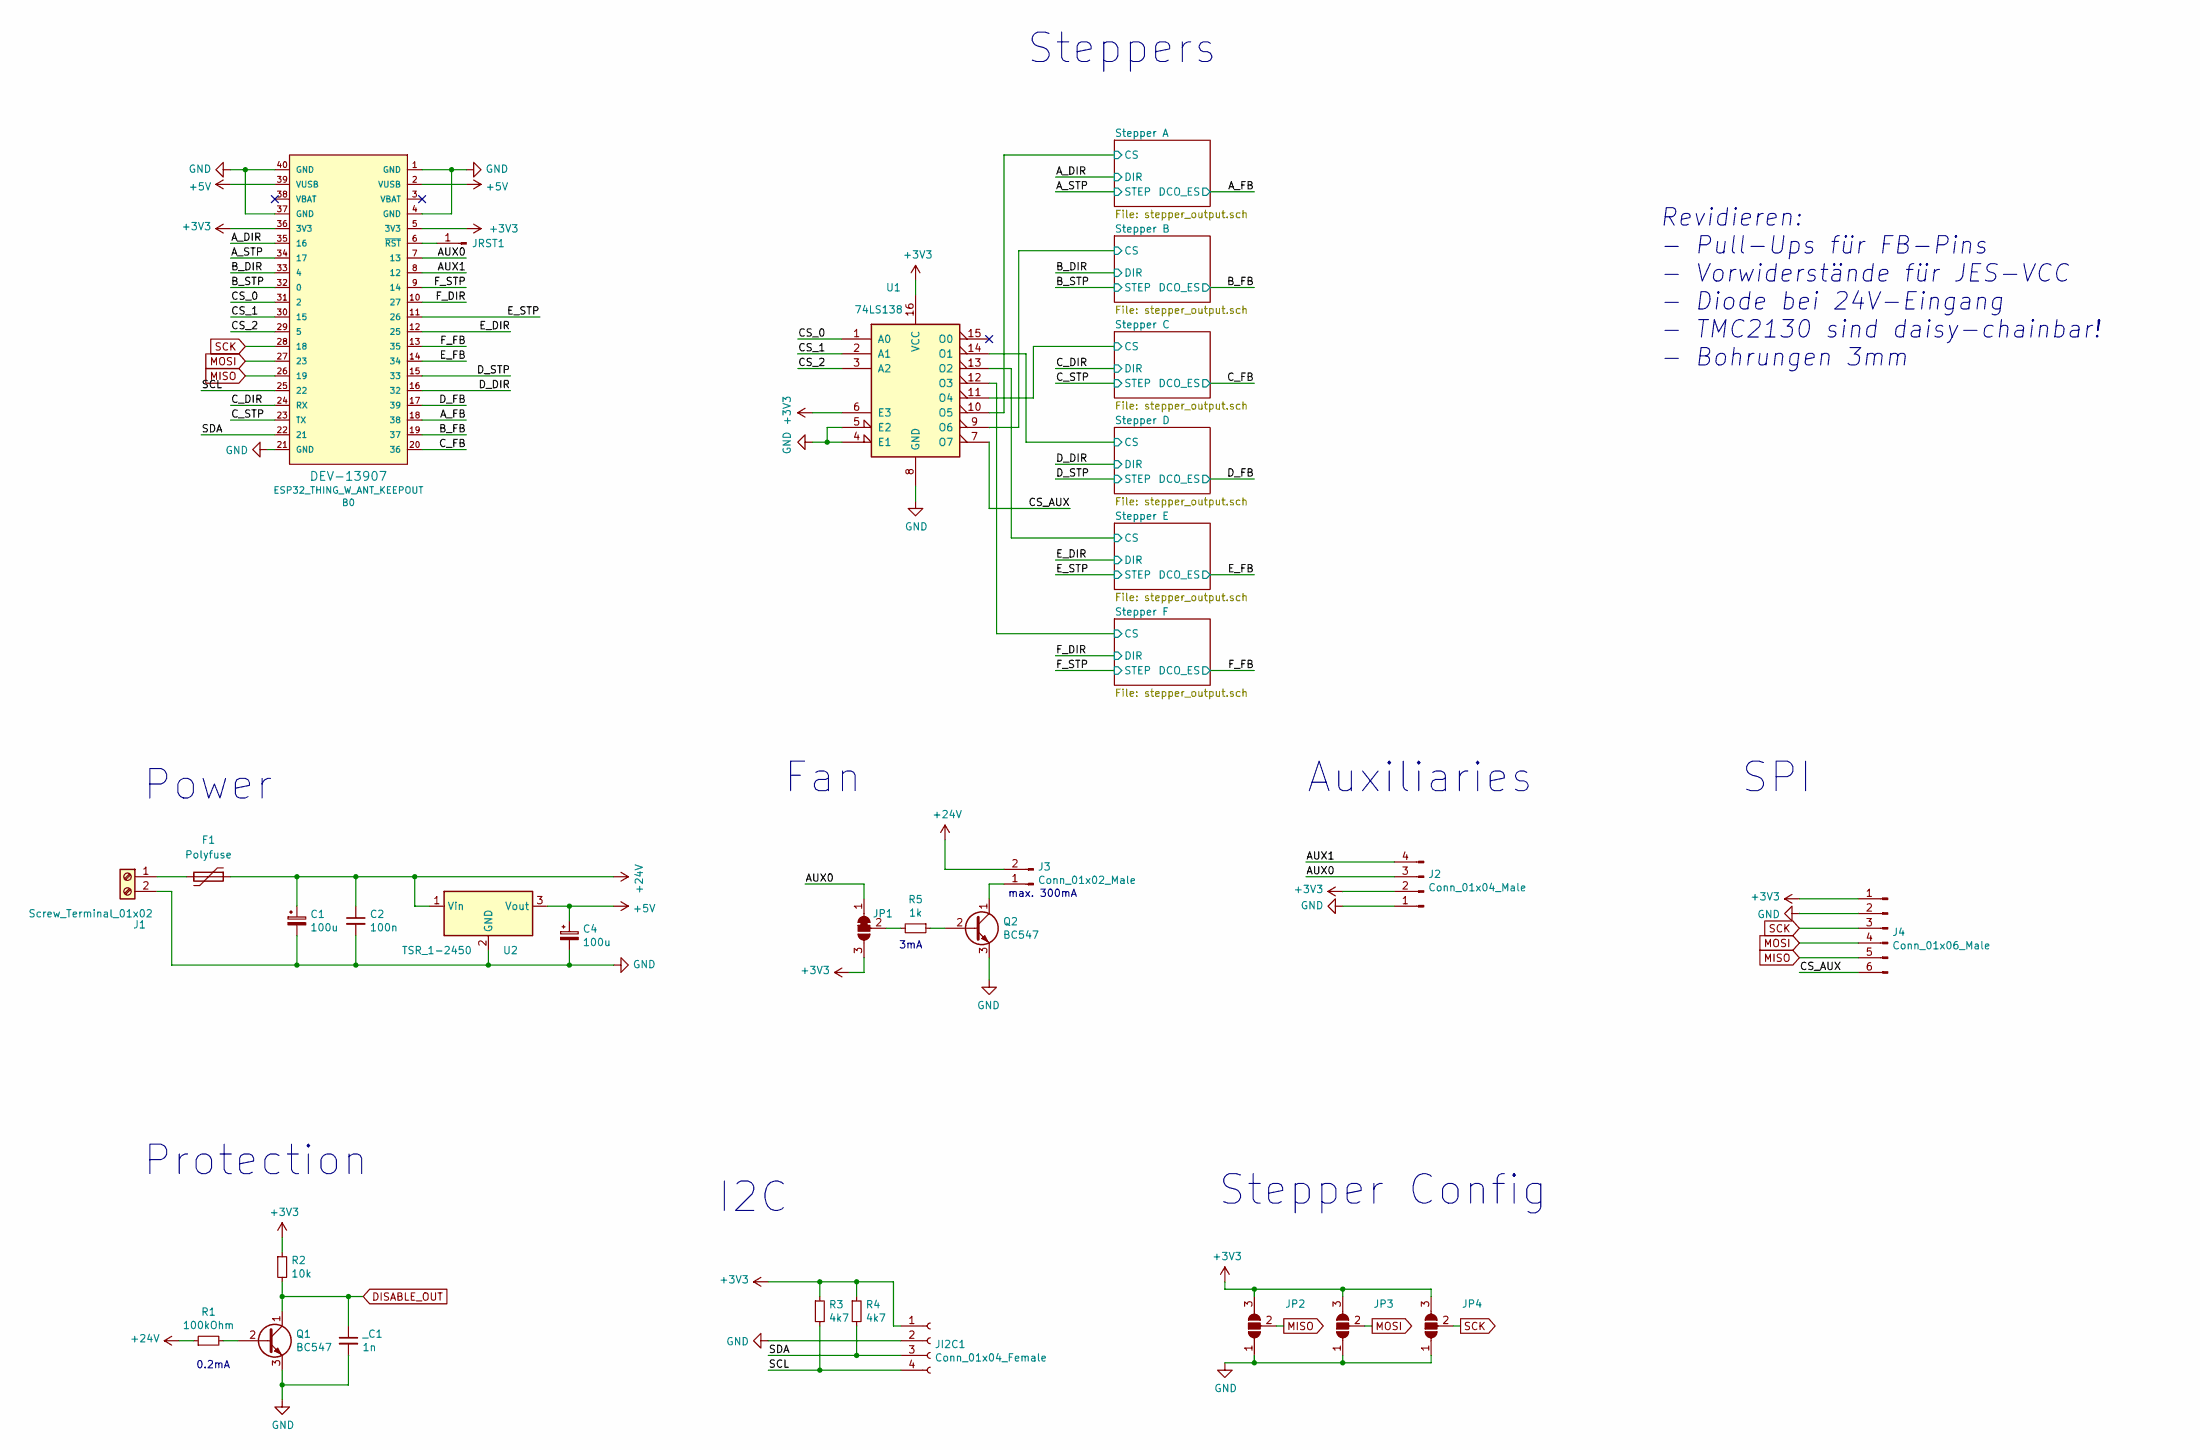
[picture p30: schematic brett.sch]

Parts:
B0: ESP32_THING_W_ANT_KEEPOUT; ESP32_THING
C1, C4: 100u; CP_Radial_D8.0mm_P3.50mm
C2: 100n; C_Radial_D6.3mm_H5.0mm_P2.50mm
F1: Polyfuse; Fuse_Bourns_MF-RHT1000
J1: Screw_Terminal_01x02; TerminalBlock_RND_205-00232_1x02_P5.08mm_Horizontal
J2: Conn_01x04_Male; PinHeader_1x04_P2.54mm_Vertical
J3: Conn_01x02_Male; PinHeader_1x02_P2.54mm_Vertical
J4: Conn_01x06_Male; PinHeader_1x06_P2.54mm_Vertical
JI2C1: Conn_01x04_Female; PinHeader_1x04_P2.54mm_Vertical
JP1: SolderJumper_3_Bridged12; SolderJumper-3_P1.3mm_Bridged12_RoundedPad1.0x1.5mm
JP2, JP3, JP4: SolderJumper_3_Open; SolderJumper-3_P1.3mm_Open_RoundedPad1.0x1.5mm
JRST1: Conn_01x01_Male; PinHeader_1x01_P2.54mm_Vertical
Q1, Q2: BC547; TO-92_Inline
R1: 100kOhm; R_Axial_DIN0207_L6.3mm_D2.5mm_P7.62mm_Horizontal
R2: 10k; R_Axial_DIN0207_L6.3mm_D2.5mm_P7.62mm_Horizontal
R3, R4: 4k7; R_Axial_DIN0207_L6.3mm_D2.5mm_P7.62mm_Horizontal
R5: 1k; R_Axial_DIN0207_L6.3mm_D2.5mm_P7.62mm_Horizontal
U1: 74LS138; DIP-16_W7.62mm
U2: TSR_1-2450; Converter_DCDC_TRACO_TSR-1_THT
_C1: 1n; C_Radial_D6.3mm_H5.0mm_P2.50mm

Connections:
+5V: B0.2 (VUSB), B0.39 (VUSB), C4.1, U2.3 (Vout)
+24V: C1.1, C2.1, F1.1, J3.2, R1.1, U2.1 (Vin); also elsewhere on the board
/AUX0: B0.7 (13), J2.3, JP1.1 (A); also elsewhere on the board
/AUX1: B0.8 (12), J2.4; also elsewhere on the board
/A_DIR: B0.35 (16); also elsewhere on the board
/A_FB: B0.18 (38); also elsewhere on the board
/A_STP: B0.34 (17); also elsewhere on the board
/B_DIR: B0.33 (4); also elsewhere on the board
/B_FB: B0.19 (37); also elsewhere on the board
/B_STP: B0.32 (0); also elsewhere on the board
/CS_0: B0.31 (2), U1.1 (A0)
/CS_1: B0.30 (15), U1.2 (A1)
/CS_2: B0.29 (5), U1.3 (A2)
/CS_AUX: J4.6, U1.7 (O7); also elsewhere on the board
/C_DIR: B0.24 (RX); also elsewhere on the board
/C_FB: B0.20 (36); also elsewhere on the board
/C_STP: B0.23 (TX); also elsewhere on the board
/D_DIR: B0.16 (32); also elsewhere on the board
/D_FB: B0.17 (39); also elsewhere on the board
/D_STP: B0.15 (33); also elsewhere on the board
/E_DIR: B0.12 (25); also elsewhere on the board
/E_FB: B0.14 (34); also elsewhere on the board
/E_STP: B0.11 (26); also elsewhere on the board
/F_DIR: B0.10 (27); also elsewhere on the board
/F_FB: B0.13 (35); also elsewhere on the board
/F_STP: B0.9 (14); also elsewhere on the board
/SCL: B0.25 (22), JI2C1.4, R3.2
/SDA: B0.22 (21), JI2C1.3, R4.2
/Stepper A/CS: U1.10 (O5); also elsewhere on the board
/Stepper B/CS: U1.9 (O6); also elsewhere on the board
/Stepper C/CS: U1.11 (O4); also elsewhere on the board
/Stepper D/CS: U1.14 (O1); also elsewhere on the board
/Stepper E/CS: U1.13 (O2); also elsewhere on the board
/Stepper F/CS: U1.12 (O3); also elsewhere on the board
DISABLE_OUT: Q1.1 (C), R2.2, _C1.1; also elsewhere on the board
MISO: B0.26 (19), J4.5, JP2.2 (C); also elsewhere on the board
MOSI: B0.27 (23), J4.4, JP3.2 (C); also elsewhere on the board
unnamed: B0.6 (~RST~), JRST1.1
unnamed: F1.2, J1.1
unnamed: J3.1, Q2.1 (C)
unnamed: JP1.2 (C), R5.2
unnamed: Q1.2 (B), R1.2
unnamed: Q2.2 (B), R5.1
SCK: B0.28 (18), J4.3, JP4.2 (C); also elsewhere on the board

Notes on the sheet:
Stepper Config
Power
I2C
Protection
Fan
3mA
max. 300mA
Auxiliaries
0.2mA
Steppers
SPI
Revidieren: - Pull-Ups für FB-Pins - Vorwiderstände für JES-VCC - Diode bei 24V-Eingang - TMC2130 sind daisy-chainbar! - Bohrungen 3mm

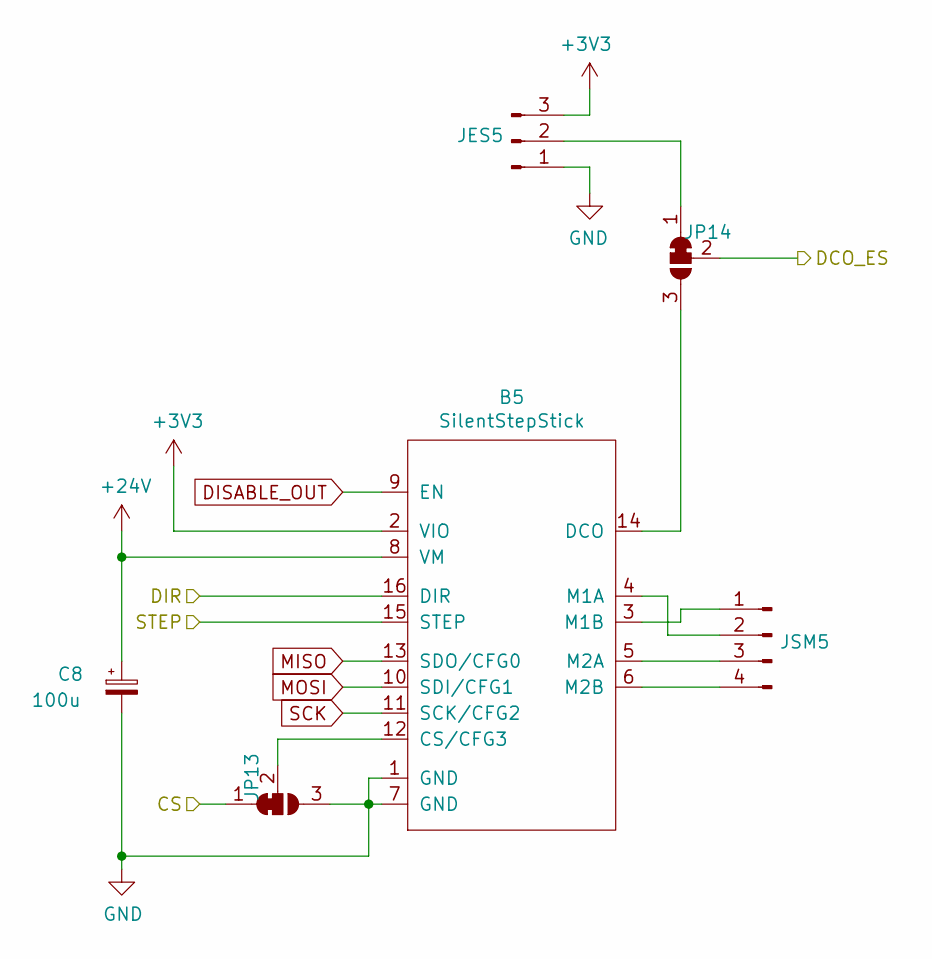
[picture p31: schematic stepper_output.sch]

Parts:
B1: SilentStepStick; StepStick
C3: 100u; CP_Radial_D8.0mm_P3.50mm
JES1: Conn_01x03_Male; PinHeader_1x03_P2.54mm_Vertical
JP8, JP9: SolderJumper_3_Bridged12; SolderJumper-3_P1.3mm_Bridged12_RoundedPad1.0x1.5mm
JSM1: Conn_01x04_Male; PinHeader_1x04_P2.54mm_Vertical

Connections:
+24V: B1.8 (VM), C3.1; also elsewhere on the board
/A_DIR: B1.16 (DIR); also elsewhere on the board
/A_FB: JP9.2 (C); also elsewhere on the board
/A_STP: B1.15 (STEP); also elsewhere on the board
/Stepper A/CS: JP8.1 (A); also elsewhere on the board
DISABLE_OUT: B1.9 (EN); also elsewhere on the board
MISO: B1.13 (SDO/CFG0); also elsewhere on the board
MOSI: B1.10 (SDI/CFG1); also elsewhere on the board
unnamed: B1.3 (M1B), JSM1.1
unnamed: B1.4 (M1A), JSM1.2
unnamed: B1.5 (M2A), JSM1.3
unnamed: B1.6 (M2B), JSM1.4
unnamed: B1.12 (CS/CFG3), JP8.2 (C)
unnamed: B1.14 (DCO), JP9.3 (B)
unnamed: JES1.2, JP9.1 (A)
SCK: B1.11 (SCK/CFG2); also elsewhere on the board

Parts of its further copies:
B2, B3, B4, B5, B6: SilentStepStick; StepStick
C5, C6, C7, C8, C9: 100u; CP_Radial_D8.0mm_P3.50mm
J5: Conn_01x03_Male; PinHeader_1x03_P2.54mm_Vertical
J6: Conn_01x04_Male; PinHeader_1x04_P2.54mm_Vertical
JES2, JES3, JES4, JES5, JES6: Conn_01x03_Male; PinHeader_1x03_P2.54mm_Vertical
JP5, JP6, JP7, JP10, JP11, JP12, JP13, JP14, JP15, JP16: SolderJumper_3_Bridged12; SolderJumper-3_P1.3mm_Bridged12_RoundedPad1.0x1.5mm
JSM2, JSM3, JSM4, JSM5, JSM6: Conn_01x04_Male; PinHeader_1x04_P2.54mm_Vertical

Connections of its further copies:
+24V: B2.8 (VM), B3.8 (VM), B4.8 (VM), B5.8 (VM), B6.8 (VM), C5.1, C6.1, C7.1, C8.1, C9.1; also elsewhere on the board
/B_DIR: B2.16 (DIR); also elsewhere on the board
/B_FB: JP6.2 (C); also elsewhere on the board
/B_STP: B2.15 (STEP); also elsewhere on the board
/C_DIR: B3.16 (DIR); also elsewhere on the board
/C_FB: JP10.2 (C); also elsewhere on the board
/C_STP: B3.15 (STEP); also elsewhere on the board
/D_DIR: B4.16 (DIR); also elsewhere on the board
/D_FB: JP12.2 (C); also elsewhere on the board
/D_STP: B4.15 (STEP); also elsewhere on the board
/E_DIR: B5.16 (DIR); also elsewhere on the board
/E_FB: JP14.2 (C); also elsewhere on the board
/E_STP: B5.15 (STEP); also elsewhere on the board
/F_DIR: B6.16 (DIR); also elsewhere on the board
/F_FB: JP16.2 (C); also elsewhere on the board
/F_STP: B6.15 (STEP); also elsewhere on the board
/Stepper B/CS: JP5.1 (A); also elsewhere on the board
/Stepper C/CS: JP7.1 (A); also elsewhere on the board
/Stepper D/CS: JP11.1 (A); also elsewhere on the board
/Stepper E/CS: JP13.1 (A); also elsewhere on the board
/Stepper F/CS: JP15.1 (A); also elsewhere on the board
DISABLE_OUT: B2.9 (EN), B3.9 (EN), B4.9 (EN), B5.9 (EN), B6.9 (EN); also elsewhere on the board
MISO: B2.13 (SDO/CFG0), B3.13 (SDO/CFG0), B4.13 (SDO/CFG0), B5.13 (SDO/CFG0), B6.13 (SDO/CFG0); also elsewhere on the board
MOSI: B2.10 (SDI/CFG1), B3.10 (SDI/CFG1), B4.10 (SDI/CFG1), B5.10 (SDI/CFG1), B6.10 (SDI/CFG1); also elsewhere on the board
unnamed: B2.3 (M1B), JSM2.1
unnamed: B2.4 (M1A), JSM2.2
unnamed: B2.5 (M2A), JSM2.3
unnamed: B2.6 (M2B), JSM2.4
unnamed: B2.12 (CS/CFG3), JP5.2 (C)
unnamed: B2.14 (DCO), JP6.3 (B)
unnamed: B3.3 (M1B), JSM3.1
unnamed: B3.4 (M1A), JSM3.2
unnamed: B3.5 (M2A), JSM3.3
unnamed: B3.6 (M2B), JSM3.4
unnamed: B3.12 (CS/CFG3), JP7.2 (C)
unnamed: B3.14 (DCO), JP10.3 (B)
unnamed: B4.3 (M1B), JSM4.1
unnamed: B4.4 (M1A), JSM4.2
unnamed: B4.5 (M2A), JSM4.3
unnamed: B4.6 (M2B), JSM4.4
unnamed: B4.12 (CS/CFG3), JP11.2 (C)
unnamed: B4.14 (DCO), JP12.3 (B)
unnamed: B5.3 (M1B), JSM5.1
unnamed: B5.4 (M1A), JSM5.2
unnamed: B5.5 (M2A), JSM5.3
unnamed: B5.6 (M2B), JSM5.4
unnamed: B5.12 (CS/CFG3), JP13.2 (C)
unnamed: B5.14 (DCO), JP14.3 (B)
unnamed: B6.3 (M1B), JSM6.1
unnamed: B6.4 (M1A), JSM6.2
unnamed: B6.5 (M2A), JSM6.3
unnamed: B6.6 (M2B), JSM6.4
unnamed: B6.12 (CS/CFG3), JP15.2 (C)
unnamed: B6.14 (DCO), JP16.3 (B)
unnamed: JES2.2, JP6.1 (A)
unnamed: JES3.2, JP10.1 (A)
unnamed: JES4.2, JP12.1 (A)
unnamed: JES5.2, JP14.1 (A)
unnamed: JES6.2, JP16.1 (A)
SCK: B2.11 (SCK/CFG2), B3.11 (SCK/CFG2), B4.11 (SCK/CFG2), B5.11 (SCK/CFG2), B6.11 (SCK/CFG2); also elsewhere on the board

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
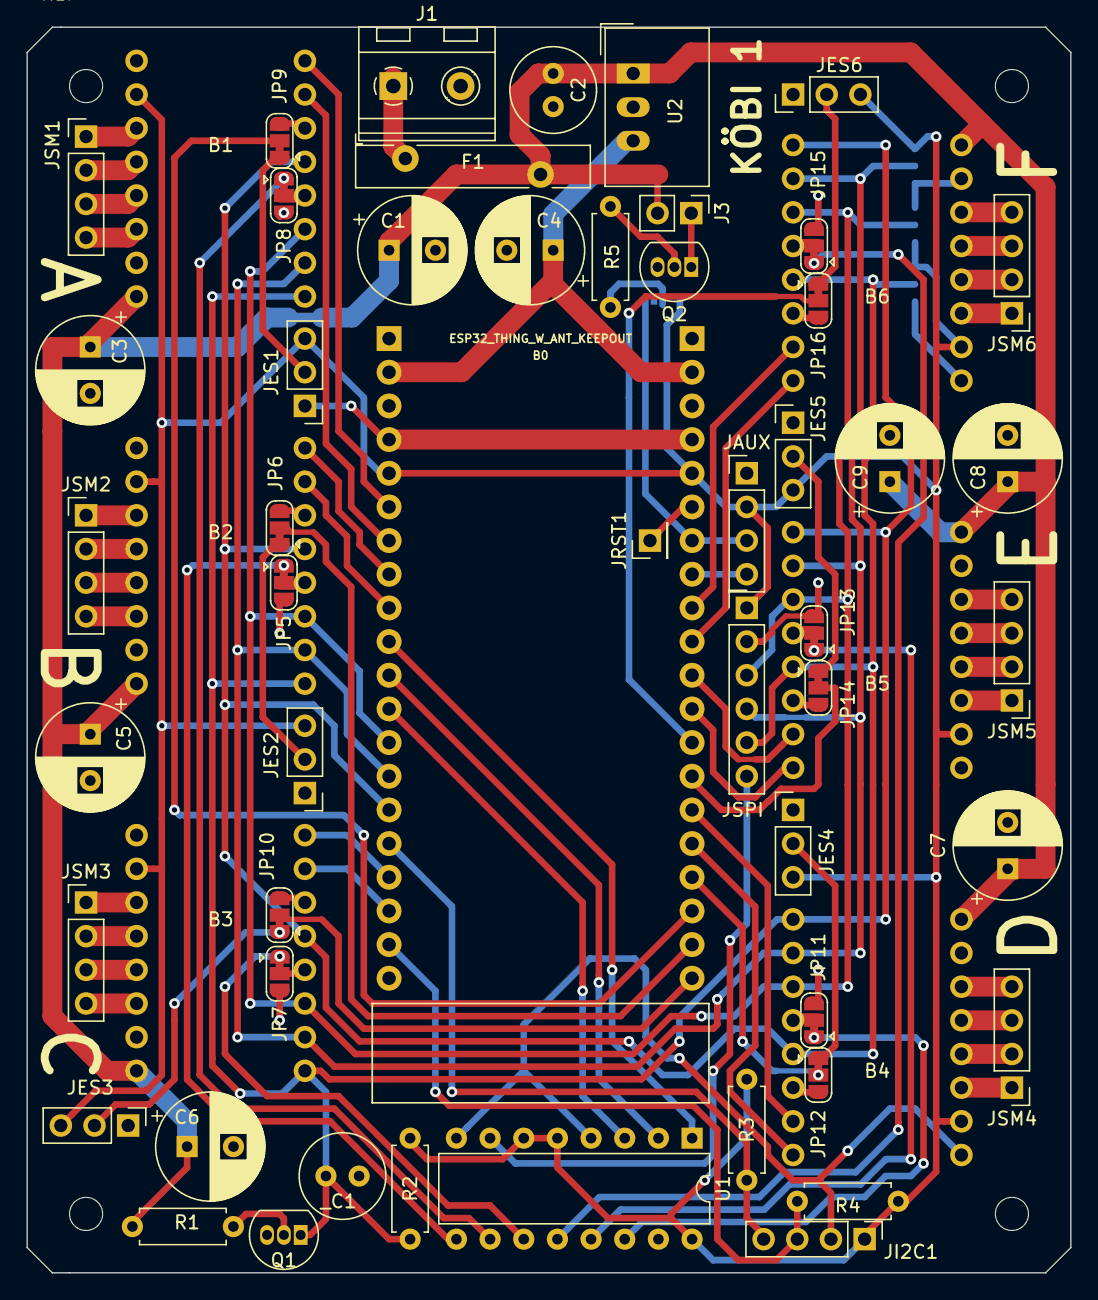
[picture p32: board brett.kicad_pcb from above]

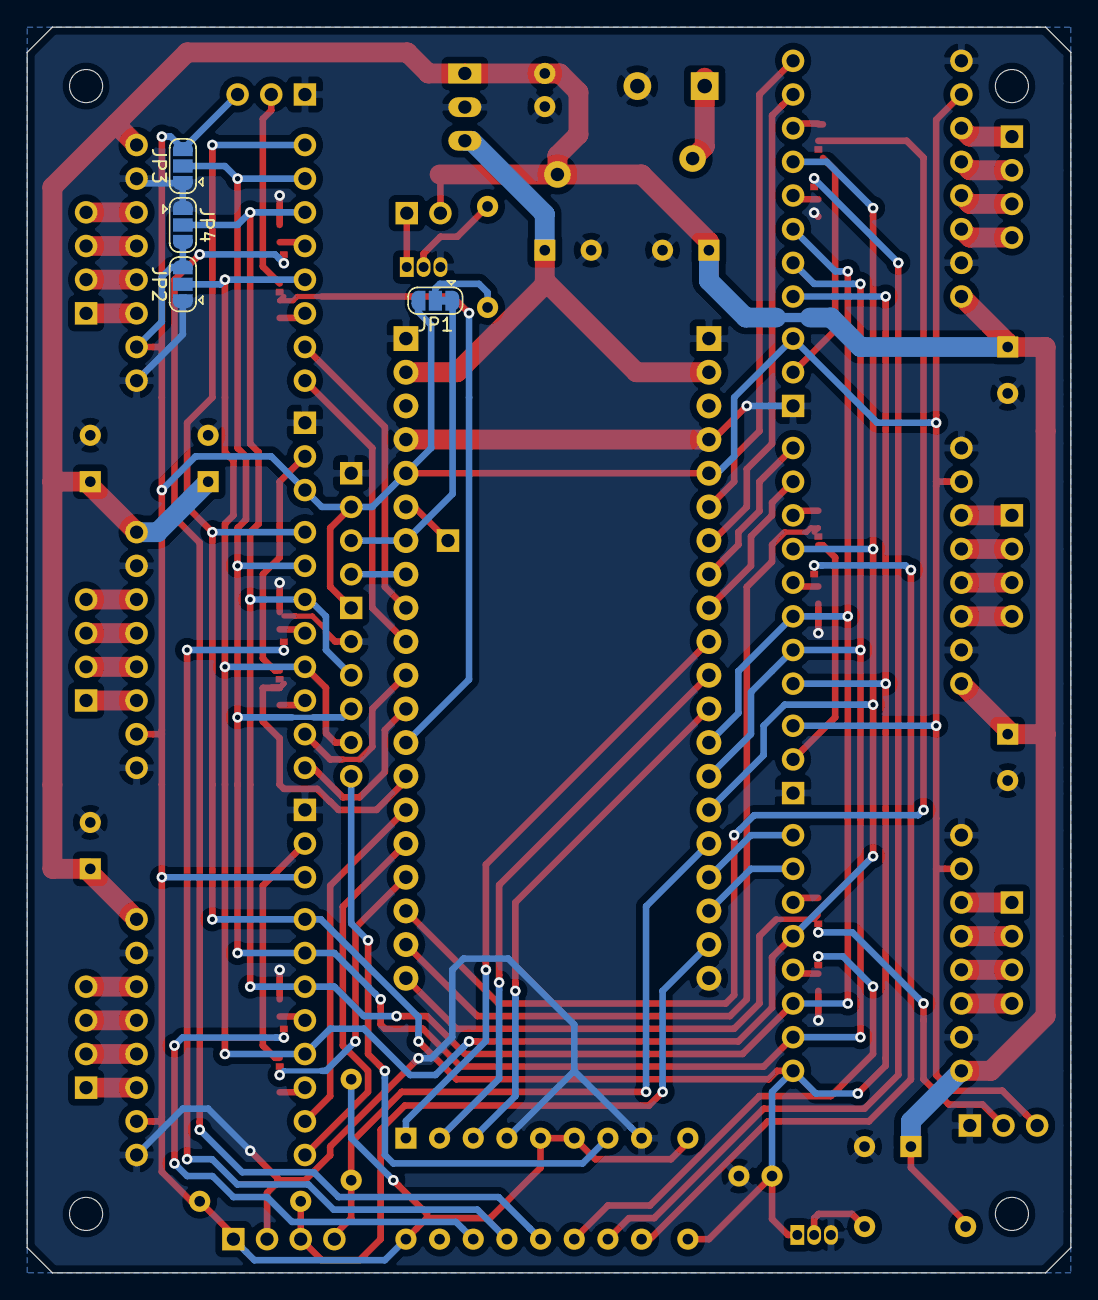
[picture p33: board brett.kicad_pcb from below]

Board: 2 copper layers, 78.7 x 94.0 mm, 61 parts (4 on the bottom side), 88 nets.

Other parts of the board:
JAUX: Conn_01x04_Male; PinHeader_1x04_P2.54mm_Vertical
JSPI: Conn_01x06_Male; PinHeader_1x06_P2.54mm_Vertical

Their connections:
/AUX0: JAUX.3; also elsewhere on the board
/AUX1: JAUX.4; also elsewhere on the board
/CS_AUX: JSPI.6; also elsewhere on the board
MISO: JSPI.5; also elsewhere on the board
MOSI: JSPI.4; also elsewhere on the board
SCK: JSPI.3; also elsewhere on the board

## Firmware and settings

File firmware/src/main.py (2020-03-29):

import micropython, gc
from machine import SPI, Pin, Timer, reset
from esp32 import MCPWM

import time

from uosc.client import Client, Bundle, create_message
from tmc_control import Tmc2130, Axis, LFO

from async_server import serve, run_server
from uasyncio import get_event_loop

from remote import Page, Control, ControlTuple, Tracker, rate_limit, Label

last_alloc = 0
def mem(label=''):
    global last_alloc
    gc.collect()
    diff = gc.mem_alloc() - last_alloc
    last_alloc = gc.mem_alloc()
    print("%20s: %4.1f    / %4.1f free" % (label, diff/1024, gc.mem_free()/1024) )

mem("imports")

fan_pin = Pin(13, Pin.OUT)
fan_pin.on()

# Check if pins 12 and 13 are connected (stepper board detection)
aux0_pin = Pin(12, Pin.IN)
on_board = True

if aux0_pin.value() != 1:
    on_board = False

fan_pin.off()
if aux0_pin.value() != 0:
    on_board = False

# Define SPI chip select pins.

cs0 = Pin(2, Pin.OUT)
cs1 = Pin(15, Pin.OUT)
cs2 = Pin(5, Pin.OUT)

def cs(idx=0):
    cs0.value(idx & 0b001)
    cs1.value(idx & 0b010)
    cs2.value(idx & 0b100)

spi = SPI(2, baudrate=1000000, polarity=1, phase=1, firstbit=SPI.MSB, sck=Pin(18), miso=Pin(19), mosi=Pin(23))

mem("spi")

dir_a = Pin(16, Pin.OUT)
pwm_a = MCPWM(0)
pwm_a.bind(Pin(17))

mem("a")

dir_b = Pin(4, Pin.OUT)
pwm_b = MCPWM(1)
pwm_b.bind(Pin(0))

mem("b")

# Activating Output C collides with UART-over-USB (same pins).
# Therefore, it is only activated when the the Jumper between pins 12 and 13 is present.
dir_c = Pin(3 if on_board else 22, Pin.OUT)
pwm_c = MCPWM(2)
pwm_c.bind(Pin(1 if on_board else 25))

dir_d = Pin(32, Pin.OUT)
pwm_d = MCPWM(3)
pwm_d.bind(Pin(33))

dir_e = Pin(25, Pin.OUT)
pwm_e = MCPWM(4)
pwm_e.bind(Pin(26))

dir_f = Pin(27, Pin.OUT)
pwm_f = MCPWM(5)
pwm_f.bind(Pin(14))

mem("d, e, f")

mem("chopper a")
chopper_a = Tmc2130(spi, (lambda: cs(5), cs))
chopper_b = Tmc2130(spi, (lambda: cs(6), cs))
chopper_c = Tmc2130(spi, (lambda: cs(4), cs))
chopper_d = Tmc2130(spi, (lambda: cs(1), cs))
chopper_e = Tmc2130(spi, (lambda: cs(2), cs))
chopper_f = Tmc2130(spi, (lambda: cs(3), cs))

mem("choppers")

a = Axis(chopper_a, dir_a, pwm_a)
b = Axis(chopper_b, dir_b, pwm_b)
c = Axis(chopper_c, dir_c, pwm_c)
d = Axis(chopper_d, dir_d, pwm_d)
e = Axis(chopper_e, dir_e, pwm_e)
f = Axis(chopper_f, dir_f, pwm_f)

mem("axes")

axes = {
    'a': a,
    'b': b,
    'c': c,
    'd': d,
    'e': e,
    'f': f
}

osc_client = None

mem("osc client")

def sing(axis, note, duration=200):
    base = 1 # cm/s
    vel = base*math.pow(2, note/12)

    axis.set_speed(vel)
    time.sleep_ms(int(duration))

    axis.set_speed(0)


class Vel(Page):

    def update_acc(self, val):
        for axis in axes.values():
            axis.acc = val
            axis.restore_acc = val

    def update_curr(self, val):
        for axis in axes.values():
            axis.chopper.set_current(val)

    def update_vel(self, val):
        for axis in axes.values():
            axis.top_speed = val
            axis.restore_top_speed = None

    def update_power(self, val):
        if val:
            [a.chopper.on() for a in axes.values()]
            self.fan.set(1)
        else:
            [a.chopper.off() for a in axes.values()]
            self.fan.set(0)

        if not on_board:
            chopper_c.off()
        print("Motors %s" % ("on" if val else "off") )


    def update_stallguard(self, val):
        for axis in axes.values():
            axis.track_load = val


    def init_controls(self):
        self.acc = Control('/all/acc', (0.1, 200), Control.QUADRATIC, action=self.update_acc, feedback=True)
        self.acc.set(80)
        self.current = Control('/all/current', (100, 1200), action=self.update_curr, feedback=True)
        self.current.set(300)
        self.vel_limit = Control('/all/vel_limit', (0, 200), Control.QUADRATIC, action=self.update_vel, feedback=True)
        self.vel_limit.set(80)

        self.reset = Control('/reset', action=lambda _: reset())
        self.fan = Control('/fan', action=fan_pin.value, feedback=True)
        self.power = Control('/power', action=self.update_power, feedback=True)

        for label, axis in axes.items():
            vel_src = Tracker(axis, 'speed')
            vel = Control('/' + label + '/vel', (None, self.vel_limit), Control.QUADRATIC, action=axis.set_speed, source=vel_src)

            def reset_for(v):
                return lambda _: v.set(0)

            stop = Control('/' + label + '/stop', (0, 1), action=reset_for(vel))
            # load = Control('/' + label + '/load', (0, 1), Tracker(axis, 'load'))

            setattr(self, 'vel_' + label, vel)
            setattr(self, 'stop_' + label, stop)
            # setattr(self, 'load_' + label, load)

        def make_noise(on):
            for axis in axes.values():
                if on:
                    axis.microstepping(6, False)
                    axis.chopper.stealthchop(False)
                else:
                    axis.microstepping(4, True)
                    axis.chopper.stealthchop(True)

        self.make_noise = Control('/all/stealthchop', action=make_noise, feedback=True)
        self.make_noise.set(0)
        self.stallguard = Control('/all/stallguard', action=self.update_stallguard, feedback=True)
        self.stallguard.set(0)

vel = Vel('velocity')



class Pos(Page):

    def init_controls(self):
        self.starts = {}
        self.ends = {}
        self.targets = {}
        self.poss = {}
        self.homes = {}

        for label, axis in axes.items():
            length = Tracker(axis, 'length')
            pos_rd = Tracker(axis, 'eff_position')
            target_tr = Tracker(axis, 'target')

            def start_for(v):
                return lambda _: v.set_zero()

            def end_for(v):
                return lambda _: v.set_length()

            def home_for(v):
                return lambda _: v.set_target(0)

            start = Control('/' + label + '/zero', action=start_for(axis))
            end = Control('/' + label + '/end', action=end_for(axis))
            target = Control('/' + label + '/target', (0, length), source=target_tr, action=axis.set_target)
            pos = Control('/' + label + '/pos', (0, length), source=pos_rd)
            home = Control('/' + label + '/home', action=home_for(axis))

            self.starts[axis] = start
            self.ends[axis] = end
            self.targets[axis] = target
            self.poss[axis] = pos
            self.homes[axis] = home

pos = Pos('position')



class XY(Page):

    def set_2d_target(self, l, r):
        if self.x:
            self.x.set_target(l)
        if self.y:
            self.y.set_target(r)

        if self.x and self.y and self.sync():
            dx = abs(self.x.target - self.x.position)
            dy = abs(self.y.target - self.y.position)

            fast = self.x if dx > dy else self.y
            slow = self.y if dx > dy else self.x

            factor = dy/dx if dx > dy else dx/dy
            print("factor for %s: %.2f" % (slow, factor))

            slow.acc = fast.acc*factor
            slow.top_speed = fast.top_speed*factor

            slow.restore_acc = fast.acc
            slow.restore_top_speed = fast.top_speed

        return


    def init_controls(self):
        self.x = None
        self.y = None

        self.sync = Control('/2dpad/sync', feedback=True)
        self.sync.set(True)

        self.pos = ControlTuple('/2dpad/pos')
        self.target = ControlTuple('/2dpad/target', action=self.set_2d_target)

        self.acc = vel.acc
        self.vel_limit = vel.vel_limit
        self.current = vel.current

        def set_x_for(axis):
            def setter(active):
                pos_control = pos.poss[axis] if active else None
                target_control = pos.targets[axis] if active else None

                self.x = axis if active else None
                self.pos.bind_left(pos_control)
                self.target.bind_left(target_control)
            return setter

        def set_y_for(axis):
            def setter(active):
                pos_control = pos.poss[axis] if active else None
                target_control = pos.targets[axis] if active else None

                self.y = axis if active else None
                self.pos.bind_right(pos_control)
                self.target.bind_right(target_control)
            return setter

        def get_x_for(axis):
            return lambda: self.x == axis

        def get_y_for(axis):
            return lambda: self.y == axis

        for label, axis in axes.items():
            x = Control('/2dpad/x/' + label, feedback=True, action=set_x_for(axis), source=get_x_for(axis))
            y = Control('/2dpad/y/' + label, feedback=True, action=set_y_for(axis), source=get_y_for(axis))
            setattr(self, 'btn_x' + label, x)
            setattr(self, 'btn_y' + label, y)


xy = XY('2dpad')

class Breath(Page):

    def update_sync(self, v):
        if v:
            self.r.freq = self.l.freq

    def update_phase(self, v):
        if not self.sync(): 
            return

        self.r.phase = self.l.phase + v


    def label_freq(self, hz):
        if hz >= 1.0:
            return "%.1f Hz" % hz

        return "%.1f s" % (1/hz)

    def toggle_for(self, lfo, axis):
        def toggle(value):
            if value:
                axis.lfos.add(lfo)
            else:
                axis.lfos.remove(lfo)

        return toggle

    def update_freq_for(self, axis):
        def update_freq(hz):
            if self.sync():
                self.l.freq = hz
                self.r.freq = hz
            else:
                axis.freq = hz
            
        return update_freq

    def update_bias_for(self, axis):
        def update_bias(bias):
            axis.center = bias

        return update_bias


    def init_controls(self):
        self.l = Axis.lfos[0]
        self.r = Axis.lfos[1]

        self.lamp = Control('/lfo/left/amplitude', (0, 30), action=lambda v: setattr(self.l, 'amp', v), mapping=Control.QUADRATIC)
        self.ramp = Control('/lfo/right/amplitude', (0, 30), action=lambda v: setattr(self.r, 'amp', v), mapping=Control.QUADRATIC)

        self.lfreq = Control('/lfo/left/frequency', (-5, 3), action=self.update_freq_for(self.l), source=Tracker(self.l, 'freq'), 
            mapping=Control.EXPONENTIAL)
        self.lfreql = Label('/lfo/left/label_frequency', self.lfreq, self.label_freq)
        self.rfreq = Control('/lfo/right/frequency', (-5, 3), action=self.update_freq_for(self.r), source=Tracker(self.r, 'freq'),
            mapping=Control.EXPONENTIAL)
        self.rfreql = Label('/lfo/right/label_frequency', self.rfreq, self.label_freq)

        self.lbias = Control('/lfo/left/bias', (0, 1), action=self.update_bias_for(self.l), source=Tracker(self.l, 'center'))
        self.rbias = Control('/lfo/right/bias', (0, 1), action=self.update_bias_for(self.r), source=Tracker(self.r, 'center'))

        self.lbiasr = Control('/lfo/left/bias_reset', action=lambda _: self.lbias.set(0.5))
        self.rbiasr = Control('/lfo/right/bias_reset', action=lambda _: self.rbias.set(0.5))

        self.lsine = Control('/lfo/left/sine', action=lambda _: self.lsaw.set(0))
        self.rsine = Control('/lfo/right/sine', action=lambda _: self.lsaw.set(0))

        self.sync = Control('/lfo/sync', action=self.update_sync, feedback=True)
        self.phase = Control('/lfo/phase', (-0.5, 0.5), action=self.update_phase)
        self.lphase = Label('/label_phase', self.phase, lambda v: "%.0f°" % (v*360))

        self.toggles = {}

        self.lfreq.set(1)
        self.rfreq.set(2)

        for label, axis in axes.items():
            toggle = Control('/lfo/left/' + label, action=self.toggle_for(self.l, axis), feedback=True)
            self.toggles['l_' + label] = toggle
            toggle = Control('/lfo/right/' + label, action=self.toggle_for(self.r, axis), feedback=True)
            self.toggles['r_' + label] = toggle


breath = Breath('lfo')


pages = [
    vel,
    pos,
    xy,
    breath
]

mem("pages")

active_page = pages[0]

def osc_handler(timetag, data):
    topic, tags, args, src = data

    values = args if args else None

    if values and len(values) == 1:
        print("(%d) %s -> %3.2f" % (len(args), topic, values[0]) )

    if topic == '/ping':
        global osc_client

        if osc_client:
            if not src == osc_client.dest:
                print('Ping received from new Address %s:%d, but ignored:' % src)
                print('GUI already bound to %s:%d.' % osc_client.dest)
            return

        print('Ping received. Binding GUI to %s:%d' % src)
        osc_client = Client(*src)

        # Switch to page 'velocity'
        bundle = Bundle()
        bundle.add(create_message('/page/velocity', 1))
        osc_client.send(bundle)

        # Signal connectivity by winking with the fan
        vel.fan.set(1)
        time.sleep_ms(500)
        vel.fan.set(0)

        return

    if topic.startswith('/page/'):
        global active_page
        page_id = topic[6:]
        matches = [page for page in pages if page.id == page_id]
        if len(matches) == 1:
            active_page = matches[0]

        else:
            print("Unknown or ambiguous page id %s." % page_id)

        print("Switching to page %s." % page_id)

        gui_update()
        return

    # Dispatch value updates
    for page in pages:
        for control in page.controls:
            control.pull(topic, values)


last_gui_update_finished = 0

def gui_update(_=None):
    if not osc_client:
        return

    global last_gui_update_finished

    now = time.ticks_ms()
    if time.ticks_diff(now, last_gui_update_finished) < 70:
        # Ensure the main loop had at least 70ms to do its input handling (etc) before the gui update is redone.
        return

    bundle = active_page.collect_updates()

    if bundle:
        #print("Bundle with %d messages" % len(bundle))
        partial = Bundle()
        for idx, update in enumerate(bundle):
            partial.add(update)
            if idx%10 == 9:
                osc_client.send(partial)
                partial = Bundle()

        osc_client.send(partial)

    last_gui_update_finished = time.ticks_ms()



gui_timer = Timer(0)
gui_timer.init(period=100, mode=Timer.PERIODIC, callback=gui_update)

mem("gui callbacks")

if __name__ == '__main__':
    local = ap.ifconfig()[0]
    loop = get_event_loop()
    loop.call_soon(run_server(local, 8000, serve, dispatch=osc_handler))
    try:
        print('Ready for WIFI connection.')
        loop.run_forever()
    except KeyboardInterrupt:
        pass
    finally:
        loop.close()

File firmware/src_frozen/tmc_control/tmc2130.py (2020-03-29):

# pylint: disable=no-member

import utime
from machine import Pin, SPI
from ustruct import pack, unpack
from machine import PWM


class Tmc2130:
    ''' A Trinamic TMC2130 stepper motor driver connected via SPI. '''


    def __init__(self, spi, chip_select):
        '''
        Connect to a TMC2130 via SPI. The passed SPI has to use SPI_MODE=3 (ie. pol=1, phs=1) and MSB-first transmission.

        ``chip_select`` can be either a hardware Pin, or a tuple of two callbacks for activating / deactivating the
        corresponding chip select line.
        The CS input on the TMC2130 is active-low. Example:

        spi = SPI(2, baudrate=1000000, polarity=1, phase=1, firstbit=SPI.MSB, sck=Pin(18), miso=Pin(19), mosi=Pin(23))
        cs_a = Pin(5, Pin.OUT)
        motor_a = Tmc2130(spi, chip_select=(cs_a.off, cs_a.on))
        TODO update

        '''

        self.spi = spi
        self._current = None

        # Chip select handlers
        if isinstance(chip_select, tuple):
            self.cs_enable = chip_select[0]
            self.cs_disable = chip_select[1]
        else:
            self.cs_enable = chip_select.off
            self.cs_disable = chip_select.on

        # Register definitions

        self.status = Register(self, None, 'Status flags from previous read access', Access.R, {
            'stst': (3, 'Standstill indicator'),
            'stallGuard': (2, 'Motor stall detected'),
            'drv_err': (1, 'Overtemperature or short circuit shutdown'),
            'reset': (0, 'IC reset occurred since last read of GSTAT')
        })
        self.__statusbyte = 0x00

        self.gconf = Register(self, 0x00, 'Global configuration flags', Access.RW, {
            'i_scale_analog': (0, 'Current scaling by analog reference'),
            'internal_Rsense': (1, 'Internal current sense resistors'),
            'en_pwm_mode': (2, 'Enable stealthChop PWM mode'),
            'shaft': (4, 'Invert shaft direction'),
            'diag0_error': (5, 'Enable DIAG0 on driver errors'),
            'stop_enable': (15, 'Emergency stop'),
        })

        self.gstat = Register(self, 0x01, 'Global status', Access.RC, {
            'reset': (0, 'IC reset occurred since last read of GSTAT'),
            'drv_err': (1, 'Indicates that the driver has been shut down due to overtemperature or short circuit detection' +
                        'since the last read access. Read DRV_STATUS for details.'),
            'cp_uv': (2, 'The internal charge pump encountered an undervoltage. In such a case, the driver is disabled')
        })

        self.ioin = Register(self, 0x04, 'Physical input pins', Access.R, {
            'step':     (0, 'STP'),
            'dir':      (1, 'DIR'),
            'dcen_cfg4':(2, 'DC_EN / CFG4'),
            'dcin_cfg5':(3, 'DCIN / CFG5'),
            'dco':      (4, 'DCO'),
            'version':  ((24, 31), 'IC version, always 17 == 0x11')
        })

        self.ihold_run = Register(self, 0x10, 'Driver current control', Access.W, {
            'ihold':        ((0, 4), 'Standstill current in units of 1/32'),
            'irun':         ((8, 12), 'Motor run current in units of 1/32'),
            'iholddelay':   ((16, 19), 'Time for motor power down transition after standstill detection ' +
                             'and TWPOWERDOWN expiration in multiples of 2^18 clock cycles.')
        })

        self.tpowerdown = Register(self, 0x11, '', Access.W, {
            'tpowerdown': ((0, 8), 'Delay for motor power down after standstill detection in multiples of 2^18 clock cycles')
        })

        self.tstep = Register(self, 0x12, 'Measured time between two 1/256 microsteps', Access.R, {
            'tstep': ((0, 20), 'Measured time between two 1/256 microsteps in units of 1/fCLK')
        })

        self.tpwmthrs = Register(self, 0x13, 'Upper velocity for stealthChop voltage PWM mode', Access.W, {
            'tpwmthrs': ((0, 20), 'tstep >= tpwmthrs => dcStep off, stealthChop PWM on'),
        })

        self.tcoolthrs = Register(self, 0x14, 'Lower velocity for coolStep and stallGuard', Access.W, {
            'tcoolthrs': ((0, 20), 'Set this par. to disable coolStep at low speeds, where it cannot work reliably')
        })

        self.thigh = Register(self, 0x15, 'Lower velocity for higher-torque stepper mode', Access.W, {
            'thigh':    ((0, 20), 'Disables coolStep, stealthChop, sets vhigh options')
        })

        self.chopconf = Register(self, 0x6C, 'Chopper and driver configuration', Access.RW, {
            'diss2g':   (30, 'Short to GND protection is: 0 = on, 1 = off'),
            'dedge':    (29, 'Enable double edge step pulses'),
            'intpol':   (28, 'Interpolation to 256 microsteps enabled'),
            'mres':     ((24, 27), 'Microstep divider. Nr of microsteps = 256/2^mres'),
            'sync':     ((20, 23), 'Pwm sync clock. Switched off above VHIGH.'),
            'vhighchm': (19, 'Switch to chm=1 and fd=0 for velocities above VHIGH.'),
            'vhighfs':  (18, 'Switch to fullstep for velocities above VHIGH.'),
            'vsense':   (17, 'Sense voltage scaling. 0 = low, 1 = high sensitivity'),
            'tbl':      ((15, 16), 'Comparator blank time. 00 = 16, 01 = 24, 10 = 36, 11 = 54 clocks'),
            'chm':      (14, 'Chopper mode. 0 = Standard (SpreadCycle), 1 = constant off time'),
            'rndtf':    (13, 'Random TOFF time. 0 = off, 1 = modulate TOFF'),
            'disfdcc':  (12, 'Fast decay mode, for chm == 1.'),
            'fd3':      (11, 'MSB of fast decay time setting TFD. Num of fast decay clock cycles = 32*TFD'),
            'hend':     ((7, 10), 'Set hysteresis low value (chm == 0) or offset (chm == 1) to -3 (0), … 12 (16)'),
            'hstrt':    ((4, 6), 'chm == 0: Add 1 … 8 to HEND; chm == 1: bits 0-2 for fast decay setting TFD. s. fd3.'),
            'toff':     ((0, 3), 'Off time (slow decay phase). 0 = Driver disable, 1 = Use only with TBL >= 2. N_clk = 12 * 32*TOFF.')
        })

        self.coolconf = Register(self, 0x6C, 'coolStep and stallGuard2 configuration', Access.W, {
            'sfilt':    (24, 'Enable LP-filter for stallGuard2 signal'),
            'sgt':      ((16, 22), 'Stall detection threshold value (signed), -64 … 63'),
            'seimin':   (15, 'Minimum current for smart current control. 0 = 1/2, 1 = 1/4 * IRUN'),
            'sedn':     ((13, 14), 'Current decrease factor'),
            'semax':    ((8, 11), 'stallGuard2 hysteresis value for smart current control'),
            'seup':     ((5, 6), 'Current increment steps per SG2-value'),
            'semin':    ((0, 3), 'Minimum sG2-value for smart current control')
        })

        # dcctrl
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

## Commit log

2019-12-16 Initial commit.
    [Redli46.stl, Sp40A.stl, bom.csv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]
2020-03-29 Bumped Submodules, new docs
    [Sp20A.stl, Sp40A.stl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]
